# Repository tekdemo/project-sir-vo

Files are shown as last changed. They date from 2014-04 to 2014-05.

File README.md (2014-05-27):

SirVo Project
=============

A servo motor replacement board that runs a magnetic encoder for continuous rotation without loss of tracking. Runs the Arduino environment on an embedded Atmega 328, exposing hardware PWM capture, I2C, and UART to a 4 wire input cable.

Additionally, allows for a header on the back of the motor controller, with the intention that you could include "backpacks" that extend the functionality much like you do with an Arduino Shield. 

Uses OpenServo board footprint, which should fit some medium size servo controllers. Tested on Parallax Continuus Rotation Servo, and looks like it should fit TowerPro MG995 servos (which require modifications for continuous rotation).

Currently in the testing phase, with several known flaws in the hardware

Known Bugs
============

- H bridge needs a proper driver for operation with higher input voltages. 

- Voltage regulator isn't performing satisfactorially, and needs to be replaced. Currently requires external 3.3V supply to function.

- Code still very unfinished (and hence, not posted). The exception is the [AS5050 Library](https://github.com/tekdemo/AS5050), which is reasonably functional.

- Motor slot alignments are still not known to function on all brands of servos, but work well for now.

- This uses a very strange passive multiplexing scheme I hacked together for the I2C and UART lines. It's been confirmed to work for UART data transmissions, but I2C is still untested.

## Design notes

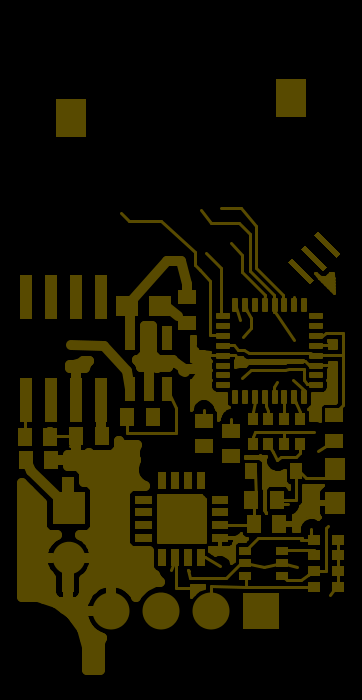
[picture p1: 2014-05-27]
gerber-previews/sirvo.v3.0.toplayer.diff.png

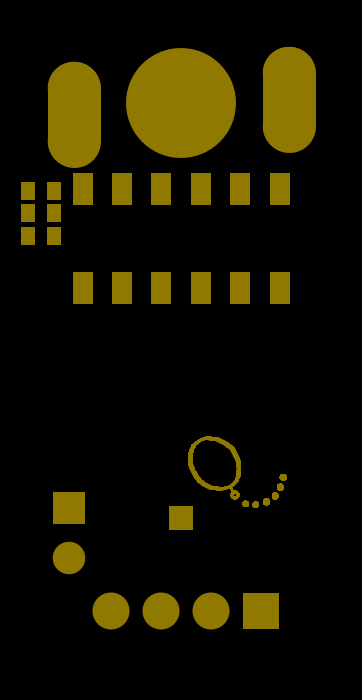
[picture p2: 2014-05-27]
gerber-previews/sirvo.v3.0.bottomstopmask.png

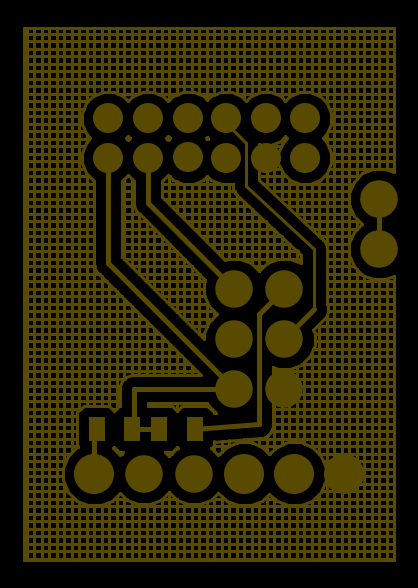
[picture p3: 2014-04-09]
gerber-previews/sirvo-breakout-shield.toplayer.png

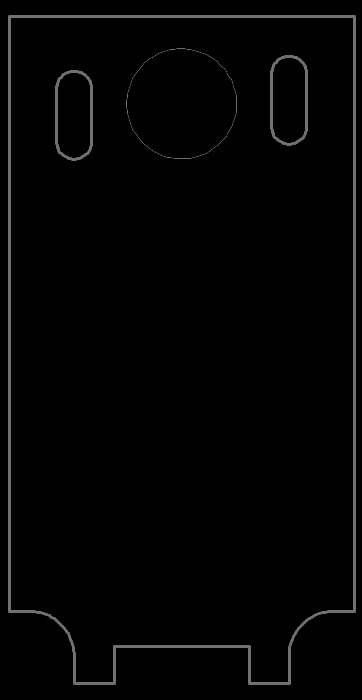
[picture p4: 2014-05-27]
gerber-previews/sirvo.v3.0.boardoutline.diff.png

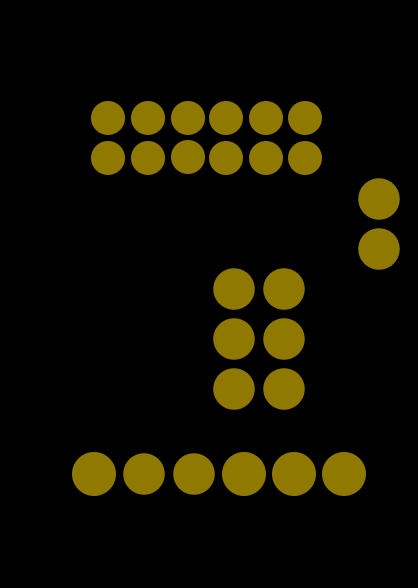
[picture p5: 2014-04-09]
gerber-previews/sirvo-breakout-shield.bottomstopmask.png

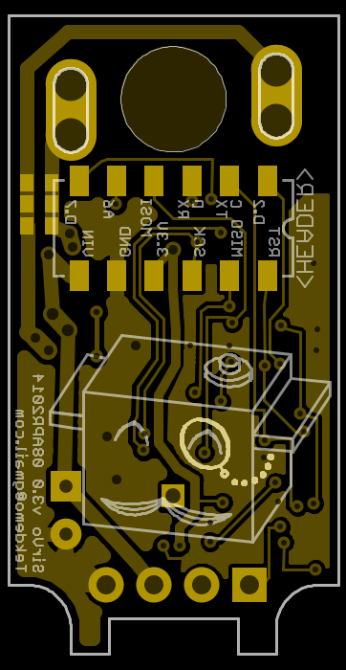
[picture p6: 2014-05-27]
gerber-previews/sirvo.v3.0.board-bottom.diff.png

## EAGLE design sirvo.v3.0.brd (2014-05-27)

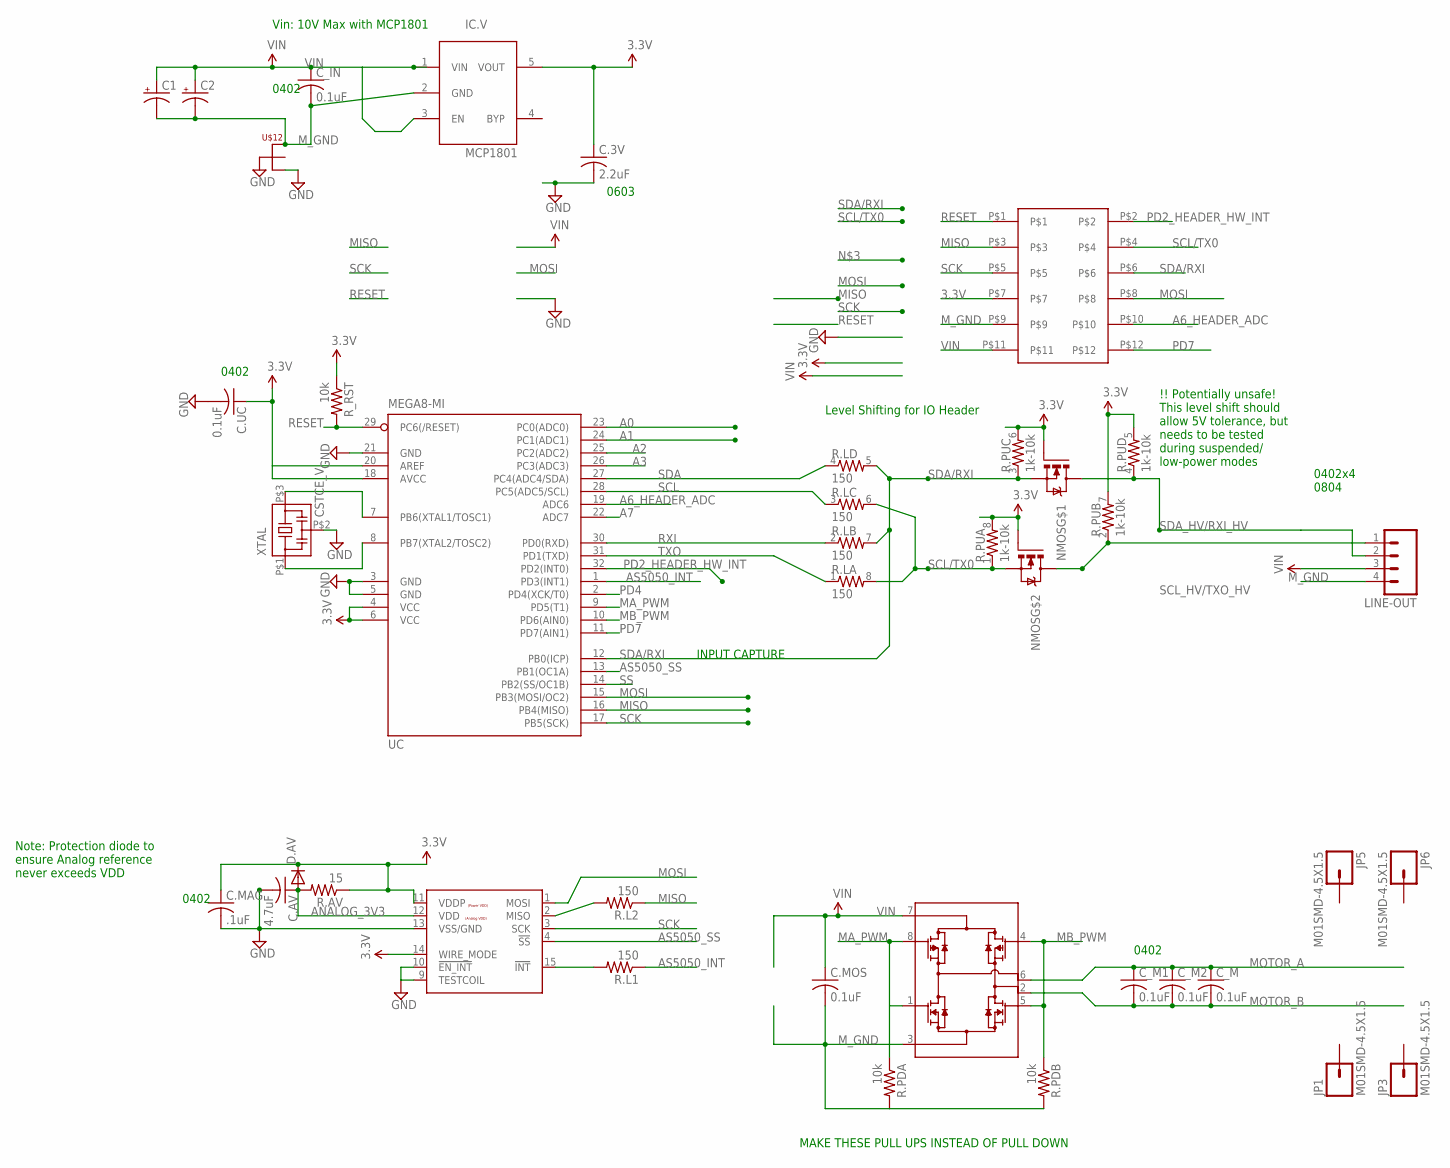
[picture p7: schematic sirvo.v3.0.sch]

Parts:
<HEADER>: M06X022MM_SMT; M2X06_SMD
C1: CAP_POLPTH2; CPOL-RADIAL-10UF-25V
C2: CAP_POLC; PANASONIC_C
C.3V: 2.2uF; C0603
C.AV: 4.7uF; C0603
C.MAG: .1uF; C0402
C.MOS, C.UC: 0.1uF; C0402
C_IN: 0.1uF; C0402
C_M, C_M1, C_M2: 0.1uF; C0402
D.AV: DIODESOD; SOD-323
IC.V: MCP1801; SOT23-5L
JP1, JP3, JP5, JP6: M01SMD-4.5X1.5; PAD-1.5X4.5
LINE-OUT: M041X04_NO_SILK; 1X04_NO_SILK
MAG: AS5050; QFN16_4X4
MOS: MOSFET-ARRAYMOSFET-ARRAY-H-BRIDGE; SO08
NMOS: MOSFET-ARRAY-PAIR; SOT-363
R.AV: 15; 0402-RES
R.L: 150; 0603-ARV
R.L1, R.L2: 150; 0402-RES
R.PDA, R.PDB: 10k; 0402-RES
R.PU: 1k-10k; 0603-ARV
R_RST: 10k; 0402-RES
U$12: NET-JUNCTION8-MIL-DIAMETER; NET-JUNCTION
UC: MEGA8-MI; MLF32
XTAL: CSTCE_V

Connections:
3.3V: <HEADER>.P$7, C.3V.1, C.MAG.1, C.UC.1, D.AV.1 (C), IC.V.5 (VOUT), MAG.11 (VDDP), MAG.14 (WIRE_MODE), NMOS.P$2 (G), NMOS.P$5 (G), R.AV.1, R.PU.5 (2), R.PU.6 (2), R.PU.7 (2), R.PU.8 (2), R_RST.1, UC.4 (VCC), UC.6 (VCC), UC.20 (AREF)
A0: UC.23 (PC0(ADC0))
A1: UC.24 (PC1(ADC1))
A2: UC.25 (PC2(ADC2))
A3: UC.26 (PC3(ADC3))
A6_HEADER_ADC: <HEADER>.P$10, UC.19 (ADC6)
A7: UC.22 (ADC7)
ANALOG_3V3: C.AV.1, D.AV.2 (A), MAG.12 (VDD), R.AV.2
AS5050_INT: R.L1.1, UC.1 (PD3(INT1))
AS5050_SS: MAG.4 (!SS), UC.13 (PB1(OC1A))
GND: C.3V.2, C.AV.2, C.MAG.2, C.UC.2, MAG.9 (TESTCOIL), MAG.10 (!EN_INT), MAG.13 (VSS/GND), U$12.P$1 (1), U$12.P$4 (3), UC.3 (GND), UC.5 (GND), UC.21 (GND), XTAL.P$2 (2)
MA_PWM: MOS.1 (N1G), MOS.8 (P1G), R.PDA.1, UC.9 (PD5(T1))
MB_PWM: MOS.4 (N2G), MOS.5 (P2G), R.PDB.1, UC.10 (PD6(AIN0))
MISO: <HEADER>.P$3, R.L2.1, UC.16 (PB4(MISO))
MOSI: <HEADER>.P$8, MAG.1 (MOSI), UC.15 (PB3(MOSI/OC2))
MOTOR_A: C_M.1, C_M1.1, C_M2.1, MOS.6 (N2D/P2D)
MOTOR_B: C_M.2, C_M1.2, C_M2.2, MOS.2 (N1D/P1D)
M_GND: <HEADER>.P$9, C1.2 (-), C2.-, C.MOS.2, C_IN.2, IC.V.2 (GND), LINE-OUT.4, MOS.3 (N1S/N2S), R.PDA.2, R.PDB.2, U$12.P$3 (2)
unnamed: UC.7 (PB6(XTAL1/TOSC1)), XTAL.P$3 (3)
unnamed: UC.8 (PB7(XTAL2/TOSC2)), XTAL.P$1 (1)
unnamed: MAG.15 (!INT), R.L1.2
unnamed: MAG.2 (MISO), R.L2.2
PD2_HEADER_HW_INT: <HEADER>.P$2, UC.32 (PD2(INT0))
PD4: UC.2 (PD4(XCK/T0))
PD7: <HEADER>.P$12, UC.11 (PD7(AIN1))
RESET: <HEADER>.P$1, R_RST.2, UC.29 (PC6(/RESET))
RXI: R.L.2 (1), UC.30 (PD0(RXD))
SCK: <HEADER>.P$5, MAG.3 (SCK), UC.17 (PB5(SCK))
SCL: R.L.3 (1), UC.28 (PC5(ADC5/SCL))
SCL/TX0: <HEADER>.P$4, NMOS.P$1 (S), R.L.6 (2), R.L.8 (2), R.PU.1
SCL_HV/TXO_HV: LINE-OUT.1, NMOS.P$6 (D), R.PU.2 (1)
SDA: R.L.4 (1), UC.27 (PC4(ADC4/SDA))
SDA/RXI: <HEADER>.P$6, NMOS.P$4 (S), R.L.5 (2), R.L.7 (2), R.PU.3 (1), UC.12 (PB0(ICP))
SDA_HV/RXI_HV: LINE-OUT.2, NMOS.P$3 (D), R.PU.4 (1)
SS: UC.14 (PB2(SS/OC1B))
TXO: R.L.1, UC.31 (PD1(TXD))
VIN: <HEADER>.P$11, C1.1 (+), C2.+, C.MOS.1, C_IN.1, IC.V.1 (VIN), IC.V.3 (EN), LINE-OUT.3, MOS.7 (P1S/P2S)

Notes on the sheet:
Level Shifting for IO Header
Vin: 10V Max with MCP1801
0402
0603
0402x4 0804
INPUT CAPTURE
Note: Protection diode to ensure Analog reference never exceeds VDD
!! Potentially unsafe! This level shift should allow 5V tolerance, but needs to be tested during suspended/ low-power modes
MAKE THESE PULL UPS INSTEAD OF PULL DOWN

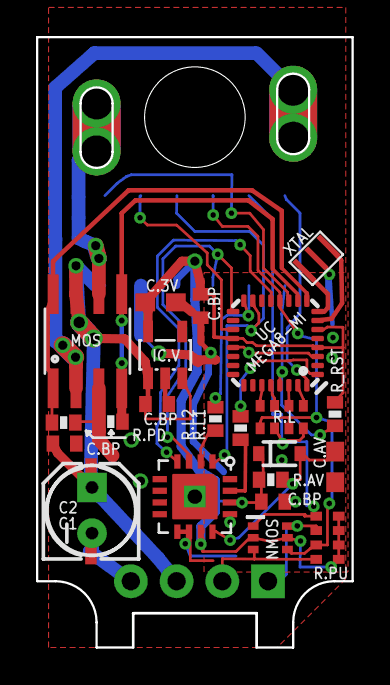
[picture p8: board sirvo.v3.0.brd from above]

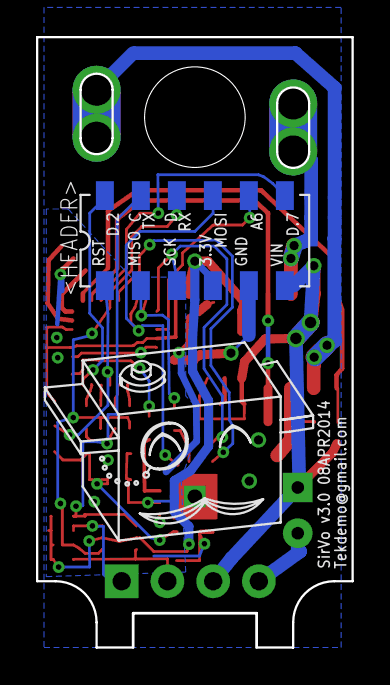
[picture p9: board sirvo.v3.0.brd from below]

Board: 2 copper layers, 17.5 x 33.9 mm, 35 parts (7 on the bottom side), 30 nets.

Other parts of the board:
U$1: LOGO-SIRVO-GOLD
U$3: SERVO-OUTLINE

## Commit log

2014-04-08 Initial rerouting, everything but header
    [sirvo.v3.0.brd, sirvo.v3.0.sch]
2014-04-08 Finished routing of all on-board signals
    Header routing not yet completed
    [sirvo.v3.0.brd, sirvo.v3.0.sch]
2014-04-08 Remove the v2.6 board file, switch to v3.0
    I know this isn't how you git, but it was an old naming scheme DON'T JUDGE ME.
    [sirvo.v2.6.brd, sirvo.v2.6.sch]
2014-04-09 Added header routing and silkscreen
    [sirvo.v3.0.brd, sirvo.v3.0.sch]
2014-04-09 Routed Headers, added header pinout in silk
    [sirvo.v3.0.brd, sirvo.v3.0.sch]
2014-04-09 Board as-ordered for revision 3.0
    [sirvo.v3.0.brd, sirvo.v3.0.sch]
2014-04-09 Update Breakout Shield for 3.0
    [sirvo-breakout-shield.brd]
2014-05-27 verified functionality of board, added notes
    [sirvo.v3.0.brd, sirvo.v3.0.sch]

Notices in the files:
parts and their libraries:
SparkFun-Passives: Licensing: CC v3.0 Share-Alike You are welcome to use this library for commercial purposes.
